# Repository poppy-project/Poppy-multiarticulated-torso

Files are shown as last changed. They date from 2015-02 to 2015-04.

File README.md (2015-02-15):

Poppy Humanoid Multi-Articulated Trunk module
===================

This Poppy module include 3D printable parts to create a robotic 5-DoFs multi-articulated trunk.

It can be used for the [Poppy Humanoid](https://github.com/poppy-project/poppy-humanoid) or be freely included in any other robotic creatures if you find it relevant.

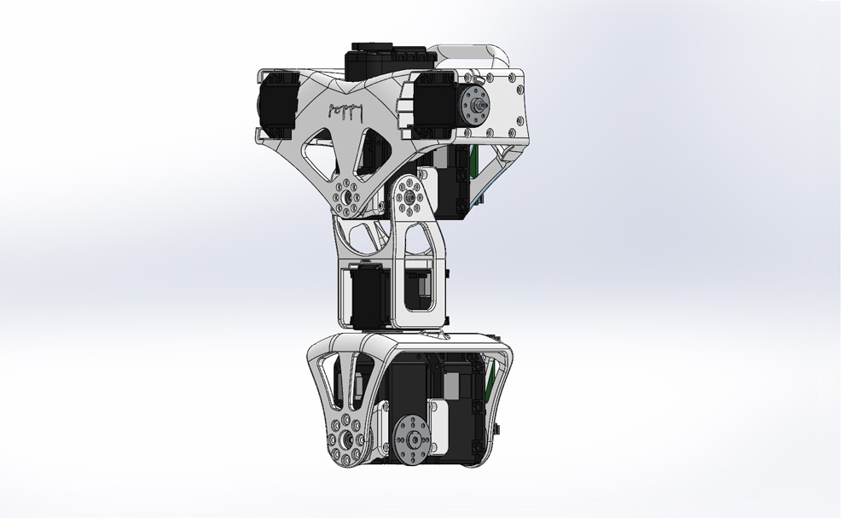
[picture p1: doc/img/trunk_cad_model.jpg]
trunk-model


The design was done using Solidworks (2013-SP5) and is distributed with native formats. More format such as STEP and STL can be found in the [release](releases/) section.

## Open Source Hardware

All the technological development work made in the Poppy project is freely available under open source licenses. Only the name usage *"Poppy"* is restricted and protected as an international trademark, please contact us if you want to use it or have more information.

 **This work is licensed under a [Creative Commons Attribution-ShareAlike 4.0 International License](http://creativecommons.org/licenses/by-sa/4.0/).**
Please keep references to the Poppy project (www.poppy-project.org) and authors when you use or fork this work.

**Authors:** Matthieu Lapeyre, Alexandre Le Falher.

## Support
You need support ?
The [Poppy forum](forum.poppy-project.org) is the best (and single) place to ask for help !

## Setup

This module requires the [Robotis Library](https://github.com/matthieu-lapeyre/Robotis-library), which includes all Robotis components needed for the actuation of this trunk.

## Contribute

### /!\ SolidWorks version
The SolidWorks policy sucks, they intentionnaly break compatibility between recent and older version. If you have a Solidworks older than 2013-SP0 you will certainly be able to open these parts but only as a read-only mode, which is equivalent to not beign able to open it...

Therefore, we won't upgrade our SolidWorks so more people can easily modify parts for their own uses.

For the same reason, we ask potential contributors wanting to pull work into official repository to downgrade (if needed) their solidworks version to 2013.

Accepting a pull-request from a Soldiworks >= 2014 will break whole compatibility.

## The Poppy project history

The Poppy project is born in 2012 in the [Flowers laboratory](flowers.inria.fr) at [Inria Bordeaux Sud-Ouest](http://www.inria.fr/en/centre/bordeaux).
It was initiated during [Matthieu Lapeyre](github.com/matthieu-lapeyre)'s PhD Thesis surpervised by [Pierre Yves Oudeyer](http://www.pyoudeyer.com/). At the beginning, the development team was composed by Matthieu Lapeyre (mechanics & design), [Pierre Rouanet](github.com/pierre-rouanet) (software) and [Jonathan Grizou](http://jgrizou.com/) (electronics).

This project is initially a fundamental research project financed by [ERC Grant Explorer](http://erc.europa.eu/) to explore the role of embodiement and morphology properties on cognition and especially on the learning of sensori-motor tasks.

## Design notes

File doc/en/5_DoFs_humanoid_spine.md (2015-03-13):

# 5 DoFs Multi-articulated Trunk assembly instructions

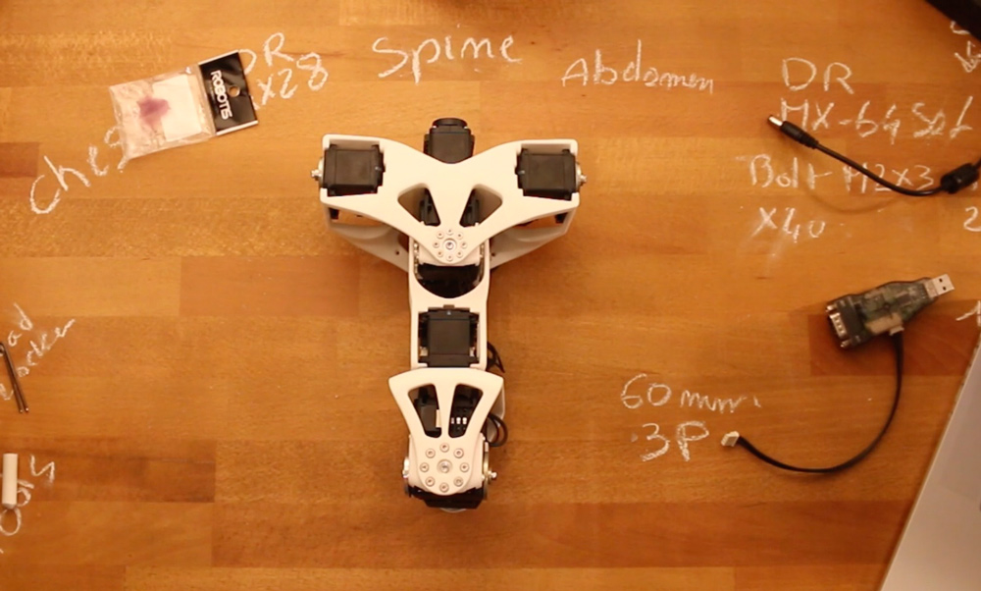
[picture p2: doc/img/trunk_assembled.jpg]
Trunk Assembled


## 1- Get all components required

First ensure you have all components detailed in the [Bill Of Material](5_DoFs_trunk_BOM.md).
Also as a friendly reminder, do not forget to use threadlocker otherwise you will see your robot disassemble itself after just few weeks due to vibration.

## 2- Build Sub-assemblies

First you need to assemble several sub-assemblies which will be combined to create the 5 DoFs Multi-articulated trunk.

The following instructions will guide you in this assembling process:

- **1.1- [Double MX64 assembly](//github.com/poppy-project/Robotis-library/blob/master/doc/en/double_MX64_assembly.md)**
- **1.2- [Double MX28 assembly](//github.com/poppy-project/Robotis-library/blob/master/doc/en/double_MX28_assembly.md)**
- **1.3- [Spine assembly](subassembly/spine_assembly_instructions.md)**
- **1.4- [Chest assembly](subassembly/chest_assembly_instructions.md)**

## 3- Multi-articulated trunk assembly

- Preparation: 10 min
- Assembly: 30-35 min

### 3.1- Requirements
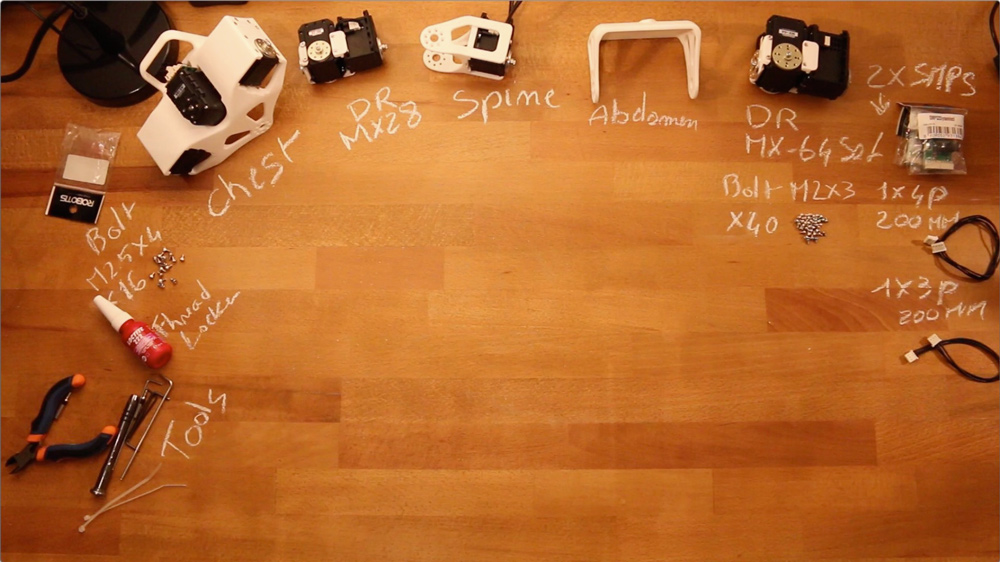
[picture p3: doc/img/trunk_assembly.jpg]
Chest Assembly


**Sub-assemblies**:
- Chest
- Double rotation MX28
- Spine
- Double rotation MX64

**3D printed parts**:
- Abdomen

**Cables**:
- 1x 4P 200mm
- 1x 3P 200mm

**Robotis parts:**
- 2x HN07-N102
- 2x SMPS2Dynamixel
- 40x Bolts M2x3
- 16x Bolts M2.5x4

**Motor configuration:**
- 1x Alimentation 12V
- 1x USB2Dynamixel or USB2AX
- A computer...

## 3.2- Assembly instructions:

- **Step 1:** Ensure you have read [**this note**](//github.com/poppy-project/Robotis-library/blob/master/doc/en/robotis_tricks.md) before continuing to avoid the classic (and critical) traps when using Robotis Dynamixel actuators.
- **Step 2**: Click on the image below to display the video:
Chest Assembly (http://youtu.be/LEHLdoBEr4Q)

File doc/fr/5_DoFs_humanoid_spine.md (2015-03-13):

# 5 DoFs Instructions d'assemblage du tronc multi-articulations

Tronc assemblé

## 1- Obtenir tous les composants requis

Premièrement, les composants sont détaillés dans la [liste des matériels](5_DoFs_trunk_BOM.md).
Note amicale, n'oubliez pas d'utiliser du freinfilet pour éviter que votre robot ne se décompose après quelques semaines d'utilisation avec des vibrations.

## 2- Construire les sous-ensembles

Tout d'abord, vous aurez besoin de plusieurs sous-ensemble que vous pourrez combiner pour créer le tronc multi-articulations.

Les instructions suivantes vous guideront dans ce processus d'assemblage :

- **1.1- [Double MX64 assembly](//github.com/matthieu-lapeyre/Robotis-library/blob/master/doc/double_MX64_assembly.md)**
- **1.2- [Double MX28 assembly](//github.com/matthieu-lapeyre/Robotis-library/blob/master/doc/double_MX28_assembly.md)**
- **1.3- [Spine assembly](subassembly/spine_assembly_instructions.md)**
- **1.4- [Chest assembly](subassembly/chest_assembly_instructions.md)**

## 3- Assemblage du tronc multi-articulations

- Préparation : 10 min
- Assemblage : 30-35 min

### 3.1- Exigences
Assemblage de la poitrine

**Sous ensembles **
- Poitrine
- MX28 à double rotation
- Colonne vertébrale
- MX64 à double rotation

**Parties 3D imprimées :**
- Abdomen

**Câbles :**
- 1x 4P 200mm
- 1x 3P 200mm

**Parties Robotis :**
- 2x HN07-N102
- 2x SMPS2Dynamixel
- 40x boulons M2x3
- 16x boulons M2.5x4

**Configuration des moteurs :**
- 1x Alimentation 12V
- 1x USB2Dynamixel or USB2AX
- Un ordinateur...

## 3.2- Instructions d'assemblage :

- **Etape 1:** En premier lieu, avant de poursuivre, assurez-vous d'avoir lu [**cette note**](//github.com/matthieu-lapeyre/Robotis-library/blob/master/doc/robotis_tricks.md) pour éviter les pièges classiques (et critiques) de l'utilisation des actionneurs des moteurs Dynamixel de Robotis.
- **Etape 2**: Cliquez sur l'image pour afficher la vidéo :
Assemblage de la poitrine (http://youtu.be/LEHLdoBEr4Q)

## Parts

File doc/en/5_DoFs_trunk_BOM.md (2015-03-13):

## Bill of Material:

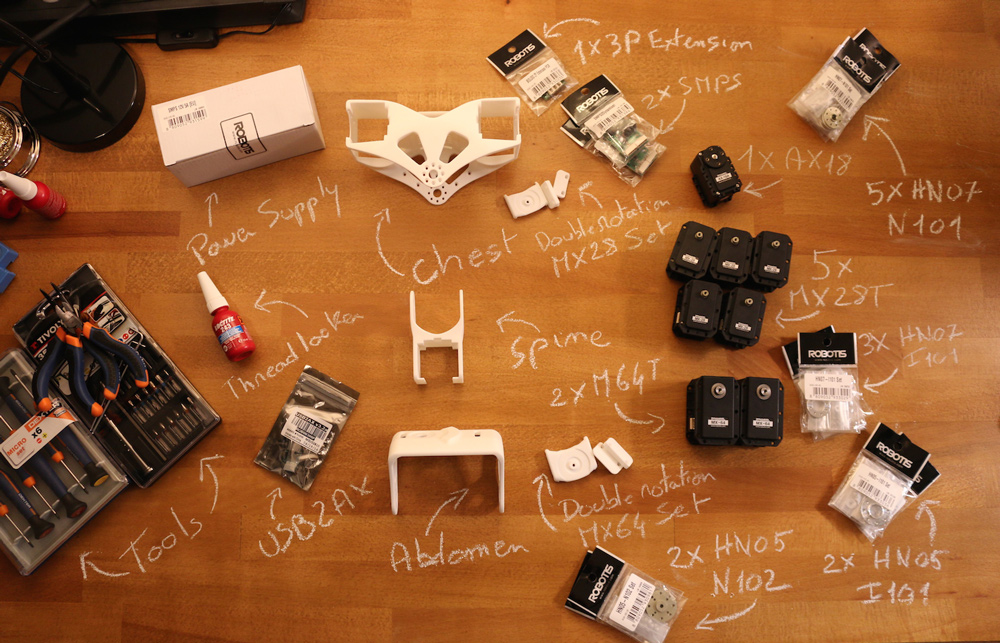
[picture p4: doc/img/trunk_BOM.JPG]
Trunk BOM


**3D Printed**:
- Chest
- Spine
- Abdomen
- Double rotation MX64 Set (3 parts)
- Double rotation MX28 Set (3 parts)

**Actuators:**
- 1x Robotis Dynamixel AX12-A (or AX18-A)
- 5x Robotis Dynamixel MX28-AT (or MX28-T)
- 2x Robotis Dynamixel MX64-AT (or MX64-T)

**Robotis parts:**
- 5x HN07-N101
- 3x HN07-I101
- 2x HN05-N102
- 2x HN05-I102
- 1x Bioloid 3P PCB HUB
- 2x SMPS2Dynamixel

**Motor configuration:**
- 1x Alimentation 12V
- 1x USB2Dynamixel or USB2AX
- A computer...

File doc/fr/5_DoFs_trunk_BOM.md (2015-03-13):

## Liste des matériels :

Liste des matériels

**Impressions 3D**:
- Poitrine
- Colonne vertébrale
- Abdomen
- Set de MX64 double rotation (3 parties)
- Set de MX28 double rotation (3 parties)

**Actionneurs :**
- 1x Robotis Dynamixel AX12-A (ou AX18-A)
- 5x Robotis Dynamixel MX28-AT (ou MX28-T)
- 2x Robotis Dynamixel MX64-AT (ou MX64-T)

**Parties Robotis :**
- 5x HN07-N101
- 3x HN07-I101
- 2x HN05-N102
- 2x HN05-I102
- 1x Bioloid 3P PCB HUB
- 2x SMPS2Dynamixel

**Configuration des moteurs :**
- 1x Alimentation 12V
- 1x USB2Dynamixel ou USB2AX
- Un ordinateur...

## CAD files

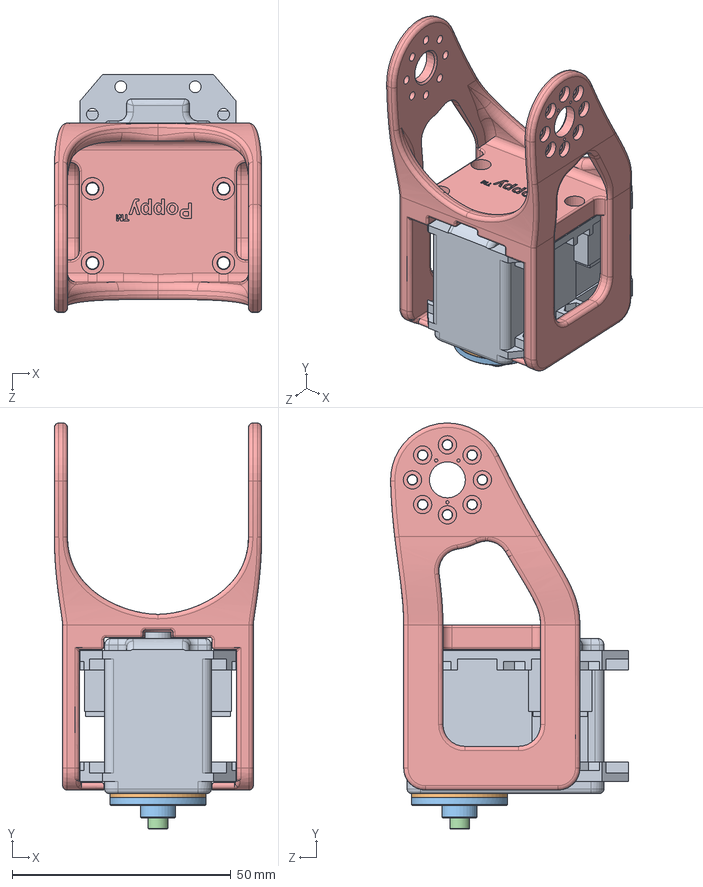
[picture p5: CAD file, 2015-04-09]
subassemblies/spine.SLDASM
47.4 x 92.8 x 54.4 mm
dynamixel_x28series
trust_washer
HN07-N101
WB_M2.5x8
spine

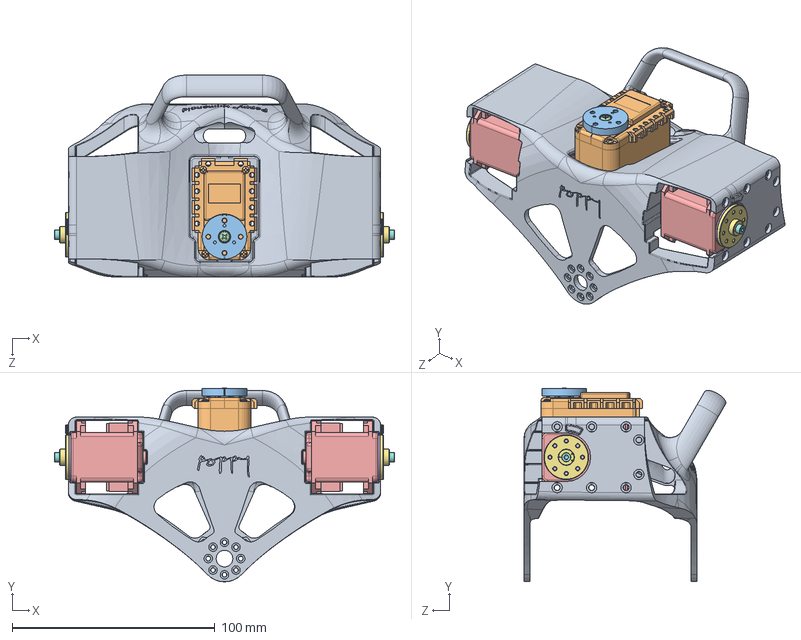
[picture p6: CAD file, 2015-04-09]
subassemblies/chest.SLDASM
167.7 x 95.6 x 99.5 mm
chest
dynamixel_AXseries
AX12_horn
BHS_M2_6X8
dynamixel_x28series x 2
trust_washer x 2
HN07-N101 x 2
WB_M2.5x8 x 2

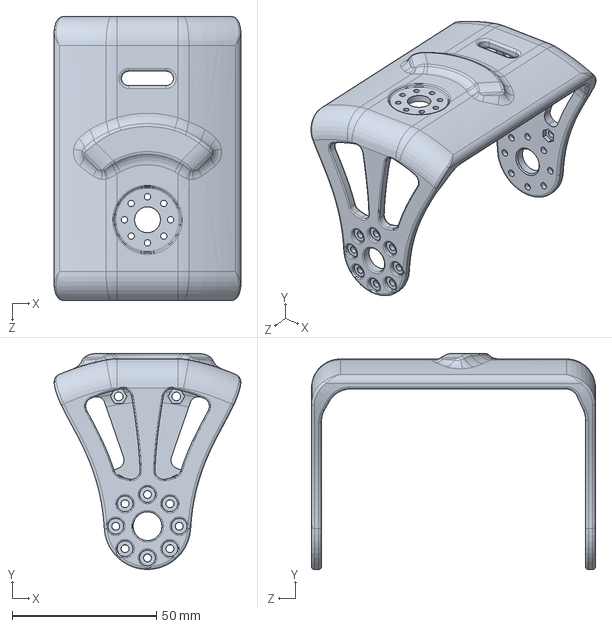
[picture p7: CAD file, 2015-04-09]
parts/abdomen.SLDPRT
64.8 x 74.9 x 98.5 mm

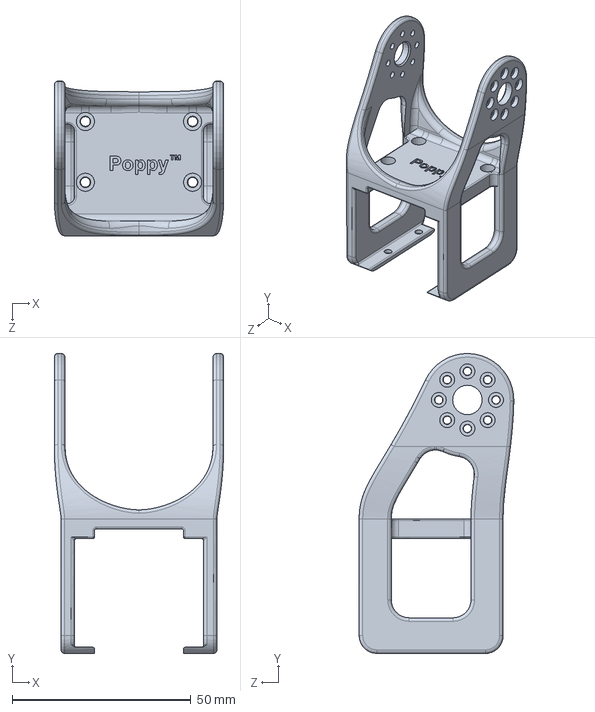
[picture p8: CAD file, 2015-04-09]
parts/spine.SLDPRT
47.4 x 83.9 x 43.3 mm

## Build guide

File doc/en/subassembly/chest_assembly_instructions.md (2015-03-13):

# Chest assembly instructions

- Preparation: 10-15 min
- Assembly: 30-45 min

## Requirement:
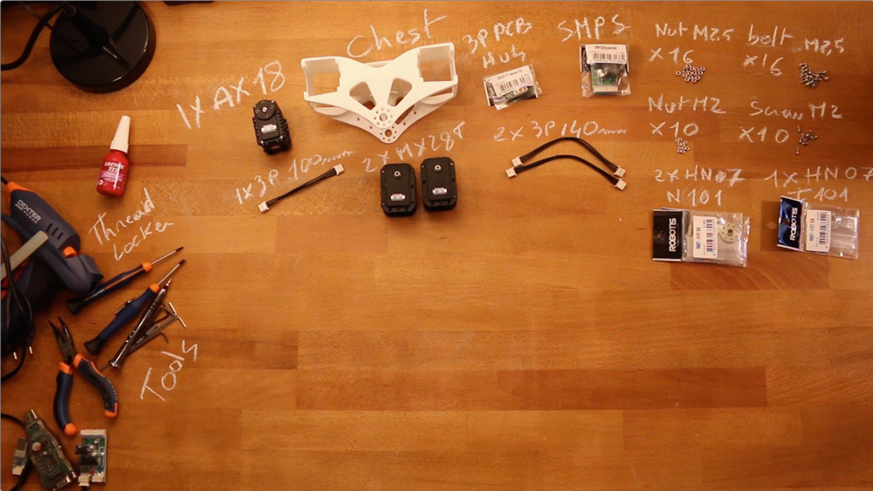
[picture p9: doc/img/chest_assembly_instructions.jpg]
Chest Assembly


**3D Printed parts**:
- Chest

**Actuators:**
- 1x Robotis Dynamixel AX12-A (or AX18-A)
- 2x Robotis Dynamixel MX28-AT (or MX28-T)

**Cables**:
- 1x 3P 100mm
- 2x 3P 140mm

**Robotis parts:**
- 2x HN07-N102
- 1x Bioloid 3P PCB HUB
- 1x SMPS2Dynamixel
- 16x Nuts M2.5
- 16x Bolts M2.5
- 10x Nuts M2
- 10x Screws M2

**Motor configuration:**
- 1x Alimentation 12V
- 1x USB2Dynamixel or USB2AX
- A computer...

## Assembly instructions:

- **Step 1:** Ensure you have read [**this note**](//github.com/poppy-project/Robotis-library/blob/master/doc/en/robotis_tricks.md) before continuing to avoid the classic (and critical) traps when using Robotis Dynamixel actuators.
- **Step 2**: Click on the image below to display the video:
Chest Assembly (http://youtu.be/qwrgV6tKTO8)

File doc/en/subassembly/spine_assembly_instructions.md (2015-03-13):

# Spine assembly instructions

- Preparation: 5 min
- Assembly: 10 min

## Requirement:
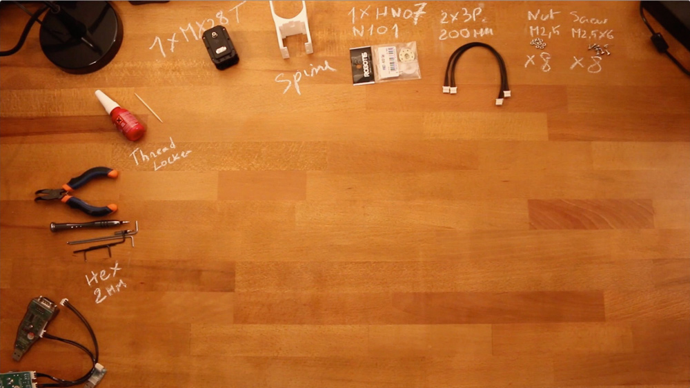
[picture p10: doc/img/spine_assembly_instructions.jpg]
Spine Assembly


**3D Printed parts**:
- Spine

**Actuators:**
- 1x Robotis Dynamixel MX28-AT (or MX28-T)

**Cables**:
- 2x 3P 200mm

**Robotis parts:**
- 1x HN07-N102
- 8x Nuts M2.5
- 8x Bolts M2.5

**Motor configuration:**
- 1x Alimentation 12V
- 1x USB2Dynamixel or USB2AX
- A computer...

## Assembly instructions:

- **Step 1:** Ensure you have read [**this note**](//github.com/poppy-project/Robotis-library/blob/master/doc/en/robotis_tricks.md) before continuing to avoid the classic (and critical) traps when using Robotis Dynamixel actuators.
- **Step 2**: Click on the image below to display the video:
Spine Assembly video (http://youtu.be/LXktU4MTITE)

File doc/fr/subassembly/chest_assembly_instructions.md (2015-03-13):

# Instructions d'assemblage de la poitrine

- Préparation : 10-15 min
- Assemblage : 30-45 min

## Exogences :
Assemblage de la poitrine

**Partie imprimées en 3D **:
- Poirtine

**Actionneurs :**
- 1x Robotis Dynamixel AX12-A (ou AX18-A)
- 2x Robotis Dynamixel MX28-AT (ou MX28-T)

**Câbles **:
- 1x 3P 100mm
- 2x 3P 140mm

**Parties Robotis :**
- 2x HN07-N102
- 1x Bioloid 3P PCB HUB
- 1x SMPS2Dynamixel
- 16x écrous M2.5
- 16x vis M2.5
- 10x écrous M2
- 10x vis M2

**COnfiguration des moteurs :**
- 1x Alimentation 12V
- 1x USB2Dynamixel or USB2AX
- Un ordinateur...

## Instructions d'assemblage :

- **Etape 1:** Assurez-vous d'avoir lu [**cette note**](//github.com/matthieu-lapeyre/Robotis-library/blob/master/doc/robotis_tricks.md) avant de continuer pour éviter les piège classique (et critiques) rencontrés lors de l'utilisation des actionneurs Robotis Dynamixel.
- **Etape 2**: Cliquez sur l'image ci-dessous pour afficher la vidéo :
Assemblage de la poitrine (http://youtu.be/qwrgV6tKTO8)

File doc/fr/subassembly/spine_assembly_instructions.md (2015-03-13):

#Instructions pour l'assemblage de la colonne vertébrale

- Préparation: 5 min
- Assemblage : 10 min

## Exigences :
Assemblage de la colonne vertébrale

**Parties imprimées en 3D**:
- Colonne vertébrale

**Actionneurs :**
- 1x Robotis Dynamixel MX28-AT (ou MX28-T)

**Câbles**:
- 2x 3P 200mm

**Parties Robotis :**
- 1x HN07-N102
- 8x écrous M2.5
- 8x vis M2.5

**Configuration des moteurs :**
- 1x Alimentation 12V
- 1x USB2Dynamixel or USB2AX
- Un ordinateur...

## Instructions d'assemblage :

- **Etape 1:** Assurez-vous d'avoir lu [**cette note**](//github.com/matthieu-lapeyre/Robotis-library/blob/master/doc/robotis_tricks.md) avant de poursuivre pour éviter les pièges classiques (et critiques) rencontrés lors l'utilisation des actionneurs Robotis Dynamixel.
- **Etape 2**: Cliquez sur l'image ci-dessous pour afficher la vidéo :
Video sur l'assemblage de la colonne vertébrale (http://youtu.be/LXktU4MTITE)

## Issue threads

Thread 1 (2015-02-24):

Thickness under bolt head M2 thickness

matthieu-lapeyre, 2015-02-24:
Reduce it from 1.5 to 1.2-1.3mm to ensure the M2x3 correct fixation.

Closed 2015-02-26.

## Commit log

2015-01-13 add all 3D printed parts for the multi-articulated torso
    [abdomen.SLDPRT, spine.SLDPRT]
2015-01-13 add multi-articulated torso subassemblies
    [chest.SLDASM, spine.SLDASM]
2015-01-13 add full assembly for the 5 DoFs Poppy Humanoid's spine
2015-02-15 add assembly instructions (not complete yet)
2015-02-19 update documentation to include stuffs about the Robotis Dynamixel assembly
2015-02-21 add link to the BOM
2015-02-26 Reduce counterbore M2 thickness Issue #1
    [spine.SLDPRT]
2015-02-26 reduce M2 counterbore thickness. Fix#1
    [abdomen.SLDPRT]
2015-04-09 update material properties
    [abdomen.SLDPRT, chest.SLDASM, spine.SLDASM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]
